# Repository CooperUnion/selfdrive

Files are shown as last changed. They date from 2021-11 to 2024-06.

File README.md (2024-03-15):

# selfdrive

> Autonomy Lab's monorepo

## Getting Started

`selfdrive` is a monorepo consisting of various Autonomy Lab projects
written in different languages with various dependencies. To avoid
dependency hell, we've opted to utilize the [Nix package manager] to
handle dependency resolution along with [direnv] to automate this
process.

### Installing Nix

Head over to <https://nixos.org/download> and proceed with the
installation for your platform. Once the process is complete, you'll
need to enable [Nix flakes] by adding the following to
`~/.config/nix/nix.conf`:

```
experimental-features = flakes nix-command
```

You'll also need to enable the unstable [channel] if you'd like to
install the latest versions of software:

```sh
$ nix-channel --add https://nixos.org/channels/nixpkgs-unstable nixpkgs
$ nix-channel --update
```

### Installing direnv

The easiest way to install [direnv] is through [`nix-env`]:

```sh
$ nix-env -iA nixpkgs.direnv
```

> Optionally, feel free to use your system's package manager to go
> through with the installation of [direnv].

Once installed, [hook direnv into your shell].

### Cloning `selfdrive`

Make sure that you've installed [Git] and [Git-LFS] before cloning.

Clone the repo:

```sh
$ git clone git@github.com:CooperUnion/selfdrive.git
```

Once cloned, make sure to initialize all the submodules:

```sh
$ git submodule update --init --recursive
```

We also recommend to configure [Git] to automatically update submodules
recursively:

```sh
$ git config --global submodule.recurse true
```

### Bootstrapping

Once everything's installed and set up, you can pass over the bootstrap
process to [direnv]:

```sh
$ direnv allow
```

If everything worked, you should be able to run [SCons] successfully:

```sh
$ scons --help
```

## Copyright & Licensing

Copyright (C) 2021--2024 Autonomy Lab

Distributed under the [GPLv3] only.

[channel]: https://nixos.wiki/wiki/Nix_channels
[direnv]: https://direnv.net/
[git]: https://git-scm.com/
[git-lfs]: https://git-lfs.com/
[gplv3]: LICENSE.md
[hook direnv into your shell]: https://direnv.net/docs/hook.html
[nix flakes]: https://nixos.wiki/wiki/Flakes
[nix package manager]: https://nixos.org/
[scons]: https://scons.org/
[`nix-env`]: https://nixos.org/manual/nix/stable/command-ref/nix-env

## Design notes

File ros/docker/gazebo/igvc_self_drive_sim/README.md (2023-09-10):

# IGVC Self-Drive Gazebo Simulator

This repository provides a Gazebo model of a Polaris GEM, as well as
worlds and models to simulate the tasks of the competition.

**If using ROS Noetic**, you need to clone the
[hector_models](https://github.com/tu-darmstadt-ros-pkg/hector_models.git)
and
[hector_gazebo](https://github.com/tu-darmstadt-ros-pkg/hector_gazebo.git)
repositories into the same workspace as this repositoriy.

After cloning into a ROS workspace along with `hector_gazebo` and
`hector_models` if necessary, run the following the command from the
root of the workspace to install additional ROS package dependencies to
make everything work correctly:

`rosdep install --from-paths src --ignore-src -r`

### Starting the Simulator

`roslaunch gazebo_ros empty_world.launch`

To load a custom Gazebo world file, pass its file path to the
`world_name` argument:

`roslaunch gazebo_ros empty_world.launch world_name:=<complete path to world file here\>`

Spawn the GEM model in Gazebo with `spawn_gem.launch` in the
`igvc_self_drive_gazebo` package:

`roslaunch igvc_self_drive_gazebo spawn_gem.launch`

The `spawn_gem.launch` file has arguments that allow the user to control
some aspects of the spawned GEM:

- `start_x`, `start_y`, `start_z`: The `x`, `y`, `z` position of the
  vehicle in Gazebo

- `start_yaw`: The direction the vehicle faces relative to the Gazebo
  world frame

- `twist_mode`: If true, the GEM subscribes to a `geometry_msgs/Twist`
  topic to move around the world. If false, it subscribes to individual
  actuator command topics. See the discussion of these modes below.

- `pub_tf`: If true, a ground truth TF transform from `world` frame to
  `base_footprint` frame is published

### Simulating IGVC Tasks

The `self_drive_tasks.world` file in the `igvc_self_drive_gazebo`
package simulates the specific tasks as described in the official rules
document, which can be found
\[[here](http://www.igvc.org/2018selfdriverules.pdf)\].

To load the world and spawn the vehicle at the starting point for a
particular task, run the corresponding launch file in the
`igvc_self_drive_gazebo` package. For example, to run task F3, the right
turn test where the vehicle has to stop at the intersection:

`roslaunch igvc_self_drive_gazebo f3_gazebo.launch`

At the moment, the F9 task is not implemented in the
`self_drive_tasks.world` Gazebo world, even though the launch file for
it exists.

### Sensor Data Topics

The following topics are published by Gazebo:

- `/fix`: GPS position given in latitude and longitude in the form of a
  `sensor_msgs/NavSatFix` message

- `/camera_front/image_raw/*`: Standard group of image topics from
  `image_proc`

- `/scan`: LIDAR scan data in the form of a `sensor_msgs/LaserScan`
  message

- `/twist`: The current measurement of the vehicle's speed and yaw rate
  in a `geometry_msgs/TwistStamped` message. The `linear.x` field
  contains the speed in m/s and `angular.z` contains the yaw rate in
  rad/s

- `/gear_state`: The current gear of the vehicle in a `std_msgs/UInt8`
  message:

  - 0 = Forward
  - 1 = Reverse

- `/sonar/*`: Group of 10 sonar sensor range measurement topics in
  separate `sensor_msgs/Range` messages. There are three sensors on the
  front of the vehicle, three on the rear, and two on either side.

### Controlling the Simulated Vehicle

The Gazebo GEM model can be controlled in two different modes:

- **Twist Mode:** Send a `geometry_msgs/Twist` message on the `/cmd_vel`
  topic with desired speed and yaw rate, and let the simulation generate
  the appropriate actuator commands.

- **Actuator Mode:** Send throttle, brake, steering, and gear actuator
  commands directly to the simulator.

#### Twist Mode (default)

The control mode is specified by setting the `twist_mode` argument to
the `spawn_gem.launch` file to true or false. This argument defaults to
true, so if you don't have to change anything to use Twist Mode.

The `linear.x` field of the user's `geometry_msgs/Twist` message should
contain the desired speed in m/s, and the `angular.z` field should
contain the desired yaw rate in rad/s.

#### Actuator Mode

By setting the `twist_mode` argument to false, the Gazebo plugin instead
subscribes to four separate actuator command topics so the user can
control them directly:

- `/throttle_cmd`: `std_msgs/Float64` topic containing commanded
  throttle percentage (0 to 1)

- `/brake_cmd`: `std_msgs/Float64` topic containing commanded brake
  torque in Newton-meters (0 to 1000)

- `/steering_cmd`: `std_msgs/Float64` topic containing commanded
  steering wheel angle in radians (-9.5 to +9.5)

- `/gear_cmd`: `std_msgs/UInt8` topic containing commanded gear, as
  controlled by the switch on the dashboard of the real vehicle:

  - 0 = Forward
  - 1 = Reverse

### Some Useful Kinematics Parameters

- Gear ratio between steering wheel and equivalent bicycle steer angle =
  17 : 1

- Wheelbase = 2.4 meters

- Track width = 1.2 meters

- Wheel radius = 0.36 meters

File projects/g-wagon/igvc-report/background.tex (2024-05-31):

\section{Background}

\subsection{Organization}

The team follows a vertically integrated structure, divided into three
disciplines consisting of three to five student groups, each led by a
subteam lead who facilitates weekly meetings. The subteams correspond
to abstract systems on the car: Hardware (Electrical + Mechanical),
Firmware, and Algorithms. In addition to weekly subteam meetings, we
hold weekly team meetings to keep everyone in the loop of new
developments and bi-weekly sprint meetings to establish tasks for our
bi-weekly test days.

The hardware subteam designs and assembles all expansion hats for the
Cooper Common Microcontroller Nodes (CCMNs), a custom
\texttt{\#coopermade} breakout board around the ESP32S3
microcontroller, to facilitate the needs of the Firmware subteam. In
addition to PCBs, the subteam is responsible for maintaining the power
distribution system of the car and designing mechanical components to
retrofit our vehicle.

Our Firmware subteam writes all our safety critical actuation code and
custom tooling to supplement software development. They aim to write
modular firmware, allowing for the fast extension of CCMNs attached to
hardware hats to specific hardware applications.

The algorithms subteam handles the perception and navigation of our
car. They create \& tune controllers, detect objects, perform
localization based on camera and encoder data, and generate paths given
all our component outputs.

\subsection{Design Assumptions \& Design Process}

Our design process revolves around ensuring our systems are safe and
easy to test in the cramped surroundings of the East Village in
downtown Manhattan. We try to make our systems as modular as possible
by breaking down every Autonomy Lab project into its various
components, allowing for overlap between different projects we may take
on. We host all our work in a publically available in a Git monorepo,
which is licensed under copyleft licenses to ensure free access to our
work to everyone. Maintaining a Git monorepo allows for easy
collaboration on components, simplifies code review, and lets us
accurately track changes to our work.

Due to Cooper's small size, it's easy for us to keep tabs on one
another to ensure things get done, but outside of meetings, we also
communicate using a Cooper-hosted instance of Matrix. We also believe
that maintaining good documentation is essential to avoid amassing
technical debt, so we keep a mix of public-facing documentation in our
monorepo and institution-specific documentation that does not make
sense to share outside Cooper.

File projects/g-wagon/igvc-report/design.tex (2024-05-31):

\section{Design}

\subsection{Mechanical}

Our mechanical design work revolved around retrofitting our vehicle so
that it's possible for it to drive itself. We added a gas-spring
emergency brake, a brake-by-cable system, spring-loaded rear encoders,
and a water-proof trunk to protect our power distribution system. In
addition to this, we designed various mounts for sensors,
microcontrollers, and our car computer. We lean towards aluminum and
steel for rigidity and machinability when designing mechanical
components to add to the car. We use 3D-printed components made from
PETG filament for anything not load-bearing, and when possible, we
drill mounting holes into our car's frame to mount components.

\subsubsection{Emergency Brake (Parking Brake)}

We mounted a gas spring rated for 20 lbs of force to our vehicle's
parking brake and we hold it in the armed position during operation
using an electromagnet. On each end of the spring, we bolted aluminum
extrusions between 3D-printed spaces that are free to rotate. We
machined brackets from 1/4" aluminum sheet metal to attach the spring
to the aluminum extrusions and hold any 3D-printed pieces to the car.

\begin{figure}[ht!]
  \centering
  
  \caption{CAD drawing of the parking brake assembly in the open position.}
\end{figure}

\subsubsection{Brake-by-Cable (BBC)}

We designed the Brake-By-Cable (BBC) system for fine control over
pressure in the master brake cylinder to better replicate a human
driver's control over the brake pedal. We designed the system based on
the constraint that it had to apply 100 lbs of force to displace the
brake pedal by two inches in less than a second. We designed the entire
assembly to fit in the small region between the master cylinder,
differential, and steering arms.

\begin{figure}[ht!]
  \centering
  
  \caption{CAD drawing of the BBC.}
\end{figure}

We chose a cable rated for 150 lbs to add a factor of safety. To reduce
our motor's torque requirements, we designed a 3:1 lever and machined
it from 1/4" steel. We connect the shorter side of the lever to the
brake pedal and the longer side to the DC motor. We machined a
three-inch steel pulley to be within the diameter recommended by the
manufacturer of our cable. We also machined an aluminum shaft coupler
to connect the top cable to our DC motor. For the DC motor, we chose it
such that the operating point of the system would be well below 20\% of
the motor's stall torque. Additionally, we added an extension spring to
the bottom of the lever to ensure that the cable stays in tension when
the motor releases the brake pedal.

We machined smaller pulleys from aluminum and used copper sleeves for
the cable terminations on the lever and brake pedal. Each termination
freely rotates using bronze bushing and shoulder bolts fastened to the
steel components. The large backplate covering the entire range of
motion of the lever is to ensure there are no pinch points in the
system. Each side of the lever also has an M6 shoulder bolt and a limit
switch so that our firmware can detect the end of the range of motion.

\subsubsection{Rear Encoder Mounts}

Critical for calculating odometry and velocity for the vehicle, this
year, we designed the rear encoders to have more precision and less
slip than the previous design. We designed and 3D printed a small wheel
(1.6 inches diameter) that directly attaches to the encoder shaft. This
wheel touches the inside of the car’s wheel so that we can measure the
tire's rotation. This geometry allows us to have over 30,000 counts per
tire rotation. To ensure that the encoder wheel does not slip and
maintains contact with the tire at all times, we designed a
spring-loaded bracket that connects with the previous encoder mount’s
bracket. The rotation point is an M8 shoulder bolt with thrust bearings
on each side of the 1/8th-inch aluminum bracket to ensure low-friction
rotation.

\begin{figure}[ht!]
  \centering
  
  \caption{CAD drawing of the rear encoders.}
\end{figure}

\subsubsection{Weather Proofing}

To protect the power distribution system from weather, we designed and
built a trunk that mounts to the back of the vehicle above the car
battery pack. We made the trunk's frame from 20mm aluminum extrusion,
held together with brackets made from a laser-cut 1/4" aluminum sheet.
We laser cut the trunk walls from 1/8" cast acrylic and fastened to the
aluminum extrusions. For ease of access, we mounted the circuit
breakers and under-voltage protection boards to the acrylic on top of
the trunk. We bolted the extrusion pieces to the chassis to ensure a
secure mount and used silicone caulk on the inside edges to ensure the
enclosure is weatherproof.

\newpage

\subsection{Electrical}

\begin{figure}[ht!]
  \centering
  
  \caption{Electric system diagram.}
\end{figure}

We distribute power from the 48V DC pack through circuit breakers,
fuses, under-voltage protection, and DC-to-DC converters to various
sensors, CCMNs, and our car computer. We daisy-chain all CCMNs with
Cat6A cables that supply 12V DC power and our car's CAN Bus. The boards
have voltage regulators, buck converters, and e-fuses for safe
operation and reverse polarity protection.

\subsubsection{Power Distribution System}

Four 12V DC, 120Ah AGM batteries connected in series power the car and
the electronic stack above. This setup yields us 5.8kWh, which lets the
car run for approximately six hours without needing to charge.

The DC motor controller (a Pololu G2 High-Power Motor Controller) draws
a lot of in-rush current when activated to drive the DC motor. To
prevent our DC motor controller from drawing too much current from the
DC-to-DC converters (causing their overcurrent protection to trip),
we've connected them to a battery charger, which charges a 12V battery
connected to our DC motor controller. We've also added a fast-burn 7A
fuse to the system to prevent damage if the motor stalls for an
extended period of time.

\subsubsection{Electronics Suite}

We connect a CCMN to an actuator, defining its node identity by its
expansion hat (if present). Each node interfaces with its actuator,
listening to control inputs over CAN and broadcasting senor values of
CAN. Webcams and our ZED2i are connected directly to our car computer.

\begin{itemize}
  \item \textbf{Accelerator:} sends two voltage signals directly to the throttle through relays to allow manual overrides.
  \item \textbf{BBC:} interfaces with a DC motor via a motor controller to perform pressure control and filters the pressure sensor before feeding it to the built-in ADC of the ESP32S3.
  \item \textbf{Encoders:} gets encoder ticks through level shifters.
  \item \textbf{Protoboard:} a generic expansion board for prototyping new expansion boards.
\end{itemize}

\subsubsection{Safety Devices}

Safety devices fall into two categories: mechanical/electrical devices
and software.

We use mechanical switches for e-stop buttons around the car to cut
power to our low-voltage system, effectively disabling all autonomous
aspects of our vehicle. Additionally, we've installed circuit breakers
around the car so that all systems have to be explicitly enabled by a
user, with the plus of adding over-current protection.

On the electrical side, we have ATC fuses in line with each device.
We've also added under-voltage protection to our 48V battery pack to
ensure its voltage does not fall below 40V and cause permanent damage.
Finally, each CCMN has a Schottky diode e-fuse on its input to allow
boards to survive accidental reverse input.

On the software side, we have a supervisor CCMN that ensures we never
latch in our vehicle's autonomous mode. This node inspects CAN messages
and, if all checks pass, can authorize other nodes on the CAN network
for autonomous control. This authorization has a TTL on the scale of
tens of milliseconds, meaning if any check fails, unauthorized
components of the system will exit autonomous control.

\subsection{Software}

Our software falls into two categories: Firmware and Algorithms.
Firmware creates the software interface between the hardware of the
car, while Algorithms generates inputs that we feed into our
Drive-By-Wire stack.

As an example, let's follow how a path generated by our Stanley
controller interacts with the car. We publish this path as a ROS topic
to another ROS node that interfaces with our CAN Bus. We then translate
this CAN message on our velocity controller CCMN using a PID controller
to a brake and throttle percentage. The throttle and BBC nodes then act
on these inputs only if authorized by our supervisor.

\subsubsection{Extracting Items from the Current Scene}

We handle object detection through a combination of a real-time
deep-learning model and an optical character recognition engine. We
chose Tesseract's OCR engine for reading road signs and only run it on
signs detected by our instance of the YOLOv8 model. We also use
point-cloud data from our ZED2i camera to compute the distance to
detected objects. Once an obstacle is detected, its location relative
to the vehicle gets published as a ROS topic.

We use two web cameras mounted on the A-pillars of our car for lane
detection. We use OpenCV to remove lens distortions and calculate a
linear mapping between pixels and physical distances. From here, we
threshold the image to detect white pixels and apply sliding windows to
find lane-line positions.

To detect which lane the car sits in, we compare the number of windows
with less than a determined number of white pixels from our sliding
windows. By nature, dashed lines have more empty windows, meaning we
can determine legal road maneuvers without a need for additional
localization.

We achieve \enquote{sensor fusion} using the
\texttt{ekf\_localization\_node} from the \texttt{robot\_localization}
ROS package. This node utilizes an extended Kalman filter to merge IMU
and encoder data for better estimates of our car's position.

\subsubsection{World Frame Representation}

We use odometry data from the \texttt{ekf\_localization\_node} to
obtain the position and orientation information of the vehicle in the
world frame. The ZED2i's point cloud data measures the vertical and
horizontal displacement of objects relative to the vehicle's location.
We then add the object's displacement relative to the vehicle's
location from its starting point to determine the object's location in
the world frame. We then feed this information into a state machine for
decision-making.

\begin{figure}[ht!]
  \centering
  
  \caption{
    We use Rviz2 to model vehicle dynamics at the control level: here,
    we demonstrate a generated path and the car position calculated
    using odometry from our rear encoders.
  }
\end{figure}

\subsubsection{Vehicle Operating Modes}

In self-driving mode, the vehicle operates in one of two states: lane
keeping or land changing. A land change generates paths to avoid road
obstructions by creating a clothoid path. We generate clothoid paths
based on the car's current position, orientation, endpoint, and final
orientation. Our vehicle switches operating modes based on the
conditions present.

\subsubsection{Trajectory Generation}

In lane-change mode, we operate purely on generated clothoid paths. A
lane change gets triggered by a detected object. Once detected, the
clothoid path gets generated and followed to avoid a collision.
Additionally, we generate trajectories to merge into different lanes or
to cross intersections.

\subsubsection{Trajectory Following Controls}

After researching trajectory-based controllers, and testing with
smaller steering robots, we determined that using a simplified bicycle
model and the Stanley geometric controller would suit our vehicle’s
needs for path following. The controller calculates a steering angle
based on two errors: the heading error, the yaw compared to the desired
heading of the path, and the cross-track error, the perpendicular
distance from the center of an axle to the path). We calculate the
steering angle using Equation \ref{eq:stanley}. Where \(\theta_e\) is
the heading error, \(t_e\) is the cross-track error, \(v\) is the
velocity, and \(k\) is the Stanley gain.

\begin{equation}
  \label{eq:stanley}
  \delta = \theta_e + \tan^{-1}\left(\frac{k t_e}{v}\right)
\end{equation}

\begin{figure}[ht!]
  \centering
  
  \caption{
    Kinematic bicycle model of a steering vehicle and the Stanley
    controller variables.
  }
\end{figure}

We have two methods of calculating the cross-track and heading errors
for the Stanley controller. For following generated paths, such as a
lane change, we use the encoders mounted to the rear tires to track the
vehicle’s current position and orientation. We calculate the Stanley
errors based on the car’s location and the nearest point of the path.

When following lane lines, when we have lines on both sides of the
vehicle, we use the web cameras mounted to the top of the vehicle to
detect the distance and angle of the lane lines relative to the car.

\subsubsection{Velocity Control}

On the Firmware side, once we receive a velocity command, the control
node determines if the car needs to accelerate or decelerate based on
the car’s current velocity. We feed the error between the desired and
actual velocities into a PID controller (the outer loop). If the car
needs to accelerate, we use a mapping between the desired acceleration
and throttle percentage and send the appropriate command to the
throttle node. If the car needs to decelerate, we use another mapping
between deceleration and brake pressure percentage and send that
command to the brake node.

On the BBC node, we implemented another PID loop (the inner loop),
which takes the error between the actual brake percentage (read by the
pressure transducer) and the desired brake percentage to calculate the
speed and direction of the BBC motor.

\begin{figure}[ht!]
  \centering
  
  \caption{Block diagram of our velocity controller.}
\end{figure}

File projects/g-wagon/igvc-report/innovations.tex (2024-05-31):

\section{Innovations}

This year, we decided to redesign our braking system and move to a
vision-based approach to path generation and object detection.

Our previous braking system, based around a Hydrastar trailer brake
system, was too powerful to allow consistent braking at low speeds. Our
new braking system, dubbed Brake-By-Cable, is our solution to add fine
control over the brakes. We installed a DC motor that rotates a pulley
so that a cable pulls on the brake pedal. We utilize a pressure and
current sensor as feedback for our control loop to allow for accurate
pressure control as requested by our vehicle controller.

To determine what lane our car is in and to calculate our heading and
cross-track errors, we've decided to use two cameras placed on each A
pillar of our vehicle. Since we can assume that our car operates on a
flat plane, we measure points along lane lines to create a trapezoidal
unwrap of each video feed, allowing us to use perspective transforms to
make an image where distance is a linear function of pixels.

\begin{figure}[ht!]
  \centering
  
  \caption{Fitted lane lines.}
\end{figure}

For our lane detection algorithm, we use a sliding window approach. We
divide the video feed from the pillar cameras into N windows, where we
threshold all white pixels within each window. We then use the
thresholded video feed to generate a polynomial model of the lane line.
This approach allows us to remove outliers and mitigate noise in our
input signals. Using these two polynomials, we can extract the
cross-track error (the distance from the center of the lane) by
comparing the distance between points on the polynomial and the front
axle. We can also extract the heading error (the angle relative to the
lane lines) by using a linear approximation of our generated
polynomials at the front axle and determining the deviation from the
vertical axis of the video feed.

\newpage

\begin{figure}[ht!]
  \centering
  
  \caption{Object detection demo.}
\end{figure}

We've also gone away with using a LIDAR sensor for object detection and
instead decided to use a deep learning model with a stereovision
camera. We're using Ultralytics's YOLOv8 model for its state-of-the-art
performance in real-time applications. We fine-tuned the model by
freezing the first ten layers and training on a small dataset of common
road obstructions and traffic signs.

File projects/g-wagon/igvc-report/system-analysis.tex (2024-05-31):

\section{System Analysis}

While testing things individually, it's easy to keep track of changes,
but once integrated into our system, it's easy to lose track of changes
and decisions. One example of this was during the development of the
BBC PCB. We broke the board into four main blocks: motor controller
logic, parking brake logic, pressure sensor data, and limit switches
for the lever's range of motion. However, when testing the entire
board, we found we would flip the polarity of certain pins, such as the
input to the motor, or flip which connectors went to the minimum limit
switch and the maximum limit switch.

The best way to prevent such mistakes is to create a more robust,
generalized system rather than case-by-case. For example, we can ensure
every wire has a proper visible label rather than memorizing its
location. Additionally, we can write out a simple checklist of what to
check before testing something. By creating a more robust system, it is
easy to prevent many of the smaller, simpler mistakes.

\subsection{Critical Hardware Failure}

One hardware failure that would prevent competition success is if an
ESP32S3 were to fail. The ESP32S3, a low-power microcontroller, limits
the amount of current it can supply. We maintain an external 12V
battery pack on the car because even though a CCMN can supply 12V, it's
limited to tens of milliamps. We handle this by using isolated circuits
to turn on/off the circuit i.e. using NMOS or PMOS transistors due to
their high input resistance as a switch or using a relay to keep the
two systems completely isolated.

\subsection{Software Development}

We store all code in a publically hosted monorepo on GitHub. We use Git
as it allows us to effectively work in parallel, while the monorepo
makes integration between various components straightforward. We
utilize GitHub features such as issues and pull requests to keep track
of problems with our code and encourage code review.

\subsection{Testing}

Before we test a particular algorithm or state machine on the car, and
because our team is limited in physical space to which we can test the
car, we test our ideas on smaller platforms, some of which we developed
within Autonomy Lab. Carrie is our designed in-house mini-car robot
platform for testing trajectory-following controllers. We tested and
tuned the Stanley geometric controller for following clothoid paths,
such as a complex path generated for parallel parking. We found the
Stanley controller to be an effective method of calculating a steering
angle for following a path. For testing with simplified dynamics, we
used a differential-drive TurtleBot platform. To initially test and
tune the OpenCV parameters for lane detection, we placed cameras on the
Turtlebot and added a simple controller to follow the lane lines.

\subsection{Physical Testing to Date}

We tested the BBC system by cycling the motor between the two limit
switches. The initial DC motor did not have enough torque and would
stall before reaching the maximum displacement of the brake pedal. We
sourced a more powerful DC motor with a higher stall torque, but this
larger motor can pull up to 25 Amps. To ensure the motor does not pull
too much current we installed a 7A fast-blow fuse on the battery
supplying power to the motor.

When measuring the pressure sensor output from the car, the original
data for the pressure sensor was from 0.7V to 2.0V. While this range of
values is valid for the ADC readings to the ESP32S3 (within 0.15V to
2.45V), there wouldn’t be enough precision to accurately calculate the
pressure percentage. By using a circuit that combines a non-inverting
OpAmp and a subtractor op amp, we simulated a circuit that linearly
remaps the pressure sensor range from 0.7V to 2.0V into 0.236V to
2.302V. In real-life however, we saw that the actual voltage range was
0.153V to 2.102V. This clearly demonstrates an example of when an ideal
simulation is different from a real-world implementation. The reason
for this difference comes from non-ideal components, device variations,
and parasitic capacitance and inductance throughout our circuit in the
op amps and resistors.

We tuned the inner PID loop for BBC using a pressure transducer and
recording the system's response time. We found that a high proportional
and small integral gain provided a fast response time with no
overshoot. When releasing the brake pedal before installing the spring,
the top cable would become loose and often fall off the pulley, causing
the cable to become plastically deformed. After installing the spring
to keep the lever and top cable in tension with the motor and pulley,
we found a great improvement in the response time and reliability of
the system.

For braking, once the inner loop's response was well tuned and we could
set and hold a desired braking percentage within 1 second, we
characterized the relationship between brake percent and deceleration.
First, we throttled the car to 10 mph, then set small increments of the
desired brake percent to measure deceleration using the encoders.

We ran tests using small increments in throttle percent to characterize
the acceleration-to-throttle percent relationship. We measured the
car's acceleration using the encoders mounted on the rear wheels.

To test the odometry for tracking position, we used Rviz2 to keep track
of the car's orientation and position relative to where it started in
the world frame. Since we could not test the throttle indoors, we
pushed the car while in neutral with the maximum steering angle to
travel in a circle to ensure the odometry returned to where we started.

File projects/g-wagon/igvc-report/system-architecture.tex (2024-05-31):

\section{System Architecture}

We like to think of our system as an hourglass. We aim to separate our
hardware components as much as possible from the algorithms we write,
where our car's firmware is the narrow bridge between these two worlds.

\vspace{1em}

Major hardware components include:
\begin{itemize}
  \item Our new Brake-By-Cable system
  \item Water-proof trunk for power distribution systems
  \item DC-DC converters
  \item Cooper Common Microcontroller Nodes
  \item A CAN Bus for node communication
  \item CCMN hats for our brakes, throttle, and encoders
  \item An ODrive for controlling our EPAS
\end{itemize}

Safety devices include:
\begin{itemize}
  \item Hardware E-STOPs around the car and inside the cabin
  \item ATC and glass tube fuses
  \item Circuit breakers
  \item Undervoltage protection
\end{itemize}

Major software modules include:
\begin{itemize}
  \item Shared firmware on all CCMNs
  \item OpenCAN for serialization/deserialization of CAN messages at cyclic
        rates
  \item Velocity and pressure controllers
  \item ROStouCAN for interfacing between nodes on our CAN Bus and our ROS
        nodes
  \item Lane detection algorithm
  \item Stanley controller for trajectory following
  \item A fine-tuned YOLO model for object detection
  \item State machines for state and event transitions based on the output of
        our object detection and lane detection
\end{itemize}

Even though we try to maintain our hourglass shape, it does not detract
from the close collaboration between our subteams. For example, our
Algorithms team needed more accurate braking on our vehicle this year,
so they met with the hardware subteam to make this possible. It was
then the responsibility of the hardware and firmware teams to work
together to ensure our new brake system performed better without
substantially changing how the system worked from the Algorithm
perspective.

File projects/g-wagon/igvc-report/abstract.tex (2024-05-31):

\begin{abstract}
  The Cooper IGVC Team is the primary research group of Cooper Union’s Autonomy
  Lab. As an organization, we're dedicated to cultivating autonomous
  vehicle research at our institution. We also work to uplift the Cooper
  community through the mentorship of underclassmen with the development
  of workshops to cultivate skills generalizable to complex projects
  outside of IGVC. We pride ourselves on building our car full-stack.
  Students in Autonomy Lab have designed all core mechanical, electronic,
  and software systems, all of which are open source.

  \vspace{1em}

  \noindent
  I, Michael Giglia, certify that the design and engineering of the vehicle by
  the current student team has been significant and equivalent to what
  might be awarded in a senior design course:

  \vspace{3em}

  \hrule

  \begin{center}
    
  \end{center}
\end{abstract}

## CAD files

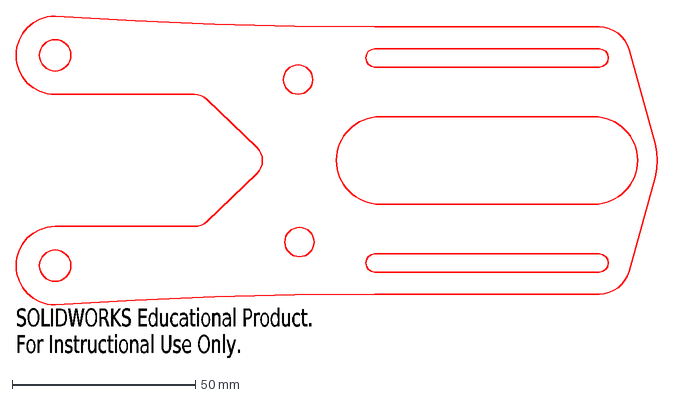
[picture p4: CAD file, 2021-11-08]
cad/encoderMount/ArmMount^EncoderMountV2.DXF
SOLIDWORKS Educational Product.
For Instructional Use Only.

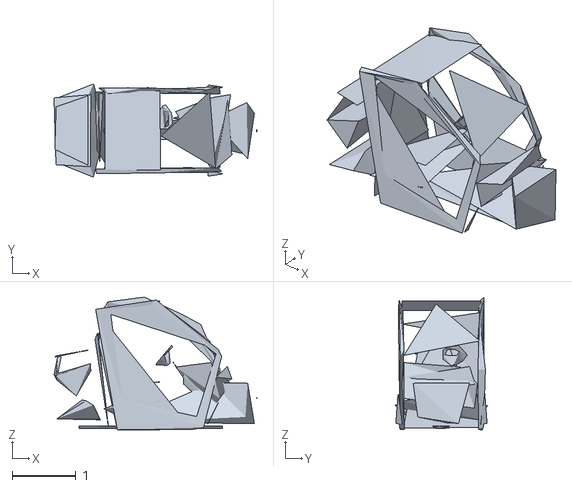
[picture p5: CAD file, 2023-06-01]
ros/docker/gazebo/igvc_self_drive_sim/igvc_self_drive_description/meshes/body_collision.stl
3.17 x 1.46 x 2.08

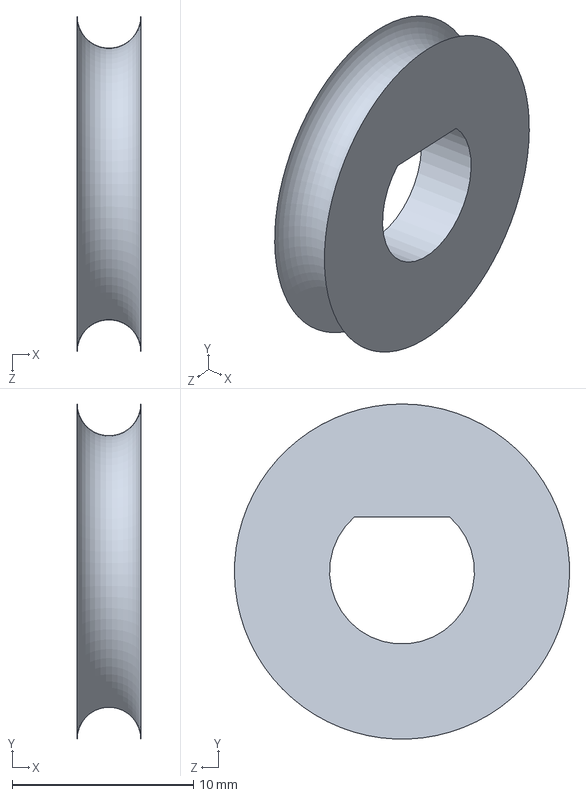
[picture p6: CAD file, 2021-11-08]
cad/encoderMount/wheel.SLDPRT
3.51 x 18.5 x 18.5 mm

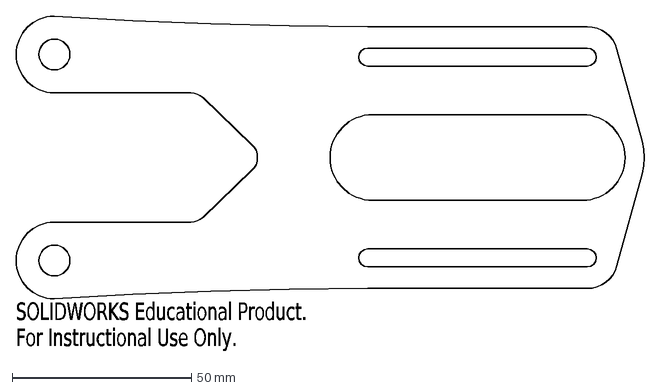
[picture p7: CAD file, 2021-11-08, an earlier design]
cad/encoderMount/ArmMount^EncoderMountV1.DXF
SOLIDWORKS Educational Product.
For Instructional Use Only.

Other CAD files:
cad/encoderMount/EncoderMountV2.SLDASM
cad/encoderMount/EncoderMountV1.SLDASM
ros/docker/gazebo/igvc_self_drive_sim/igvc_self_drive_gazebo/models/ocean/mesh.blend

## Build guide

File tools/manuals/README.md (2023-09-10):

# Notes

- The GEM service manual says -2019 and our GEM is a 2020 model, but the
  dealer says it's the same manual.

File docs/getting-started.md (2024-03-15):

# Getting Started

[`selfdrive`] is a rather *complicated* repo.

If you've never worked on a project of this scale, it can be daunting to
know where to start. The goal of this guide is to give you enough of a
foothold to start asking the right questions and to begin your adventure
here at Autonomy Lab.

## Fundamentals

Before we even get to cloning [`selfdrive`], you need to have the basic
mechanical skills required to traverse a shell. [MIT's Missing Semester]
serves as a great starting point for just this. The following table
lists the lectures you should watch if you plan to work on a specific
Autonomy Lab group:

| Lecture | Hardware | Firmware | Algorithms |
| --- | --- | --- | --- |
| [Course overview + the shell] | ✓\* | ✓\* | ✓\* |
| [Shell Tools and Scripting] | ✓ | ✓\* | ✓\* |
| [Editors (Vim)] | | | |
| [Data Wrangling] | | ✓ | ✓\* |
| [Command-line Environment] | ✓ | ✓\* | ✓\* |
| [Version Control (Git)] | ✓\* | ✓\* | ✓\* |
| [Debugging and Profiling] | | ✓ | ✓ |
| [Metaprogramming] | | ✓ | ✓ |
| [Security and Cryptography] | | | |
| [Potpourri] | | ✓ | ✓ |
| [Q&A] | | ✓ | ✓ |

> *Note: an `*` denotes you should also do the associated exercises.*

At a minimum, to clone [`selfdrive`], you should watch and do the
exercises for [Course overview + the shell] and [Version Control (Git)],
as these lectures provide you the fundamentals to hit the ground
running.

## System Configuration

Since [`selfdrive`] consists of software written in different
programming languages with a wide variety of dependencies, we've made an
effort to make getting your machine ready as painless as possible with
the [Nix package manager] and [direnv]. You can find cloning
instructions and system setup information on the repo's [`README.md`].

## Repo Layout

> Currently, [`selfdrive`] does not respect this structure. We're in the
> process of migrating over to this layout. Sorry for the time being.

```
selfdrive/
+-- can/
|   +-- network.yml
|
+-- docs/
|
+-- components/
|   +-- component/
|   |   +-- docs/
|   |   +-- src/
|   |   +-- component.toml
|   |
|   +-- ...
|
+-- lib/
|
+-- projects/
|   +-- project/
|   |   +-- docs/
|   |   +-- project.toml
|   |
|   +-- ...
|
+-- ...
```

There's quite a bit to unpack here, so let's get to it!

### [`components/`]

The [`components/`] directory contains components that serve as the
building blocks of a project.

Each component has a `docs/` directory that contains [symlinks] to
relevant documentation. These symlinks need to stay up to date as they
will automatically get triggered for manual review on pull requests to
ensure that documentation stays up to date. Having these symlinks also
ensures that anyone who wishes to get up to speed on a component has a
quick list of relevant documentation to read.

The `src` directory contains the source files. The contents and layout
of this directory highly depend on the component language(s) and use
case. It is best to see existing components to get a feel for it.

Finally, `component.toml` contains metadata related to the component.

### [`can/`]

[`can/`] describes the CAN networks of our projects. Here, you'll find
definitions for networks, messages, and signals for [OpenCAN] to
process.

### [`docs/`]

The [contributing guidelines] cover the structure for documentation. You
may notice that it closely follows the structure of [`selfdrive`]
itself.

### [`lib/`]

The [`lib/`] directory contains shared libraries used in components.
Since these are generalized pieces of software, the contents of each
directory can wildly vary. Feel free to explore these directories if
you're curious.

### [`projects/`]

The [`projects/`] directory contains projects that are composed of
various components. Like a component, each project has a `docs/`
directory with symlinks to relevant documentation and a `project.toml`
with related metadata.

### What About Everything Else?

It'd be impractical to cover every last file and directory in
[`selfdrive`]. Unfortunately, there's no shortcut to knowing where you
can find everything or how various bits of code interact, but there are
tools that can help!

- [`fd`]: a simple, fast and user-friendly alternative to `find`
- [`fzf`]: a command-line fuzzy finder
- [`rg`]: ripgrep recursively searches directories for a regex pattern

## So What's Next?

Now that you have a general idea of how [`selfdrive`] works, it's time
to move on to group-specific getting started guides. Feel free to move
along to these without finishing all of the suggested [missing semester]
lectures; however, understand they do nothing but benefit you!

[command-line environment]: https://missing.csail.mit.edu/2020/command-line/
[contributing guidelines]: contributing.md#directory-structure
[course overview + the shell]: https://missing.csail.mit.edu/2020/course-shell/
[data wrangling]: https://missing.csail.mit.edu/2020/data-wrangling/
[debugging and profiling]: https://missing.csail.mit.edu/2020/debugging-profiling/
[direnv]: https://direnv.net/
[editors (vim)]: https://missing.csail.mit.edu/2020/editors/
[metaprogramming]: https://missing.csail.mit.edu/2020/metaprogramming/
[missing semester]: https://missing.csail.mit.edu/
[mit's missing semester]: https://missing.csail.mit.edu/
[nix package manager]: https://nixos.org/
[opencan]: https://github.com/opencan
[potpourri]: https://missing.csail.mit.edu/2020/potpourri/
[q&a]: https://missing.csail.mit.edu/2020/qa/
[security and cryptography]: https://missing.csail.mit.edu/2020/security/
[shell tools and scripting]: https://missing.csail.mit.edu/2020/shell-tools/
[symlinks]: https://en.wikipedia.org/wiki/Symbolic_link
[version control (git)]: https://missing.csail.mit.edu/2020/version-control/
[`can/`]: https://github.com/CooperUnion/selfdrive/tree/dev/can
[`components/`]: https://github.com/CooperUnion/selfdrive/tree/dev/components
[`docs/`]: https://github.com/CooperUnion/selfdrive/tree/dev/docs
[`fd`]: https://github.com/sharkdp/fd
[`fzf`]: https://github.com/junegunn/fzf
[`lib/`]: https://github.com/CooperUnion/selfdrive/tree/dev/lib
[`projects/`]: https://github.com/CooperUnion/selfdrive/tree/dev/projects
[`readme.md`]: https://github.com/CooperUnion/selfdrive/blob/dev/README.md
[`rg`]: https://github.com/BurntSushi/ripgrep
[`selfdrive`]: https://github.com/CooperUnion/selfdrive

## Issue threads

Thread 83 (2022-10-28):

Missing EEPROM IC causes node to crash

dmezh, 2022-10-28:
We currently have EEPROM disabled because boards with a missing EEPROM crash. The EEPROM driver should be made resilient to this condition and indicate an error when needed.

dmezh, 2023-02-05:
See #113

jacobkoziej, 2023-11-01:
The following has been addressed by 3e016b3

Closed 2023-11-01.

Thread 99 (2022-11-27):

Report Core Temperature on CAN on Node v1.2

dmezh, 2022-11-27:
ESP32-S3 has a core temperature sensor: https://docs.espressif.com/projects/esp-idf/en/v4.4.2/esp32s3/api-reference/peripherals/temp_sensor.html

Report the temperature on CAN. Please ping me to discuss how to unify the CAN message between 1.1 and 1.2, since 1.1 doesn't have a temp sensor.

jacobkoziej, 2023-11-01:
Resolved in #130

Closed 2023-11-01.

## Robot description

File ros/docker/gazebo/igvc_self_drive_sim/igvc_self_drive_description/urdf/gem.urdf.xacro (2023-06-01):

<?xml version="1.0"?>

<robot name="gem" xmlns:xacro="http://ros.org/wiki/xacro">

  <xacro:include filename="$(find igvc_self_drive_description)/urdf/gem_gazebo.urdf.xacro"/>
  <xacro:include filename="$(find igvc_self_drive_description)/urdf/gem_sensors.urdf.xacro"/>

  <xacro:property name="half_front_track_width" value="0.6" />
  <xacro:property name="half_rear_track_width" value="0.6" />
  <xacro:property name="half_wheelbase" value="1.2" />
  <xacro:property name="wheel_radius" value="0.32" />
  <xacro:property name="wheel_thickness" value="0.17" />
  <xacro:property name="wheel_mass" value="10.0" />
  <xacro:property name="body_mass" value="544.0" />
  <xacro:property name="body_width" value="${2*half_rear_track_width}" />
  <xacro:property name="body_depth" value="${2*half_wheelbase + 0.8}" />
  <xacro:property name="body_length" value="0.6" />

  <xacro:macro name="rear_wheel" params="name x y z flip" >
    <link name="wheel_${name}" >
      <visual>
        <origin xyz="0 0 0" rpy="0 ${flip * pi - pi/2} 0" />
        <geometry>
          <mesh filename="package://igvc_self_drive_description/meshes/wheel.dae" scale="2.54 2.54 2.54" />
        </geometry>
      </visual>

      <collision>
        <geometry>
          <cylinder radius="${wheel_radius}" length="${wheel_thickness}" />
        </geometry>
      </collision>

      <inertial>
        <origin xyz="0 0 0" rpy="0 0 0"/>
        <mass value="${wheel_mass}"/>
        <inertia ixx="${wheel_mass/12*(3*wheel_radius*wheel_radius + wheel_thickness*wheel_thickness)}" ixy="0" ixz="0" iyy="${wheel_mass/12*(3*wheel_radius*wheel_radius + wheel_thickness*wheel_thickness)}" iyz="0" izz="${wheel_mass/2 * wheel_radius*wheel_radius}"/>
      </inertial>

    </link>
    <joint name="wheel_${name}_joint" type="continuous" >
      <parent link="base_link" />
      <child link="wheel_${name}" />
      <origin xyz="${x} ${y} ${z}" rpy="-1.57079632679 0 0" />
      <axis xyz="0 0 1" />
      <limit effort="1000.0" velocity="22.0" />
    </joint>
  </xacro:macro>

  <xacro:macro name="front_wheel" params="name x y z flip" >
    <link name="wheel_${name}" >
      <visual>
        <origin xyz="0 0 0" rpy="0 ${flip * pi - pi/2} 0" />
        <geometry>
          <mesh filename="package://igvc_self_drive_description/meshes/wheel.dae" scale="2.54 2.54 2.54" />
        </geometry>
      </visual>

      <collision>
        <geometry>
          <cylinder radius="${wheel_radius}" length="${wheel_thickness}" />
        </geometry>
      </collision>

      <inertial>
        <origin xyz="0 0 0" rpy="0 0 0"/>
        <mass value="${wheel_mass}"/>
        <inertia ixx="${wheel_mass/12*(3*wheel_radius*wheel_radius + wheel_thickness*wheel_thickness)}" ixy="0" ixz="0" iyy="${wheel_mass/12*(3*wheel_radius*wheel_radius + wheel_thickness*wheel_thickness)}" iyz="0" izz="${wheel_mass/2 * wheel_radius*wheel_radius}"/>
      </inertial>
    </link>

    <link name="steer_${name}" >
      <inertial>
        <origin xyz="0 0 0" rpy="0 0 0"/>
        <mass value="20.0"/>
        <inertia ixx="0.1" ixy="0" ixz="0" iyy="0.1" iyz="0" izz="0.1"/>
      </inertial>
    </link>

    <joint name="steer_${name}_joint" type="revolute" >
      <parent link="base_link" />
      <child link="steer_${name}" />
      <origin xyz="${x} ${y} ${z}" rpy="0 0 0" />
      <axis xyz="0 0 1" />
      <limit upper="0.6" lower="-0.6" effort="0.0" velocity="0.0" />
    </joint>

    <joint name="wheel_${name}_joint" type="continuous" >
      <parent link="steer_${name}" />
      <child link="wheel_${name}" />
      <origin xyz="0 0 0" rpy="-1.57079632679 0 0" />
      <axis xyz="0 0 1" />
      <limit effort="1000.0" velocity="22.0" />
    </joint>
  </xacro:macro>

  <link name="base_footprint">
  </link>

  <link name="base_link">
    <inertial>
      <origin xyz="0 0 0.75" rpy="0 0 0"/>
      <mass value="${body_mass}"/>
      <inertia ixx="${body_mass/12 * (body_width*body_width + body_length*body_length)}" ixy="0" ixz="0" iyy="${body_mass/12 * (body_length*body_length + body_depth*body_depth)}" iyz="0" izz="${body_mass/12 * (body_width*body_width + body_depth*body_depth)}"/>
    </inertial>
    <visual>
      <origin xyz="-0.22 0 0.07" rpy="0 0 0"/>
      <geometry>
        <mesh filename="package://igvc_self_drive_description/meshes/body.dae" scale="1 1 1" />
      </geometry>
    </visual>
    <collision>
      <origin xyz="-0.22 0 0.07" rpy="0 0 0"/>
      <geometry>
        <mesh filename="package://igvc_self_drive_description/meshes/body_collision.stl" scale="1 1 1" />
      </geometry>
    </collision>
  </link>

  <xacro:rear_wheel name="rl" x="${-half_wheelbase}" y="${half_rear_track_width}" z="0" flip="1" />
  <xacro:rear_wheel name="rr" x="${-half_wheelbase}" y="${-half_rear_track_width}" z="0" flip="0" />
  <xacro:front_wheel name="fl" x="${half_wheelbase}" y="${half_front_track_width}" z="0" flip="1" />
  <xacro:front_wheel name="fr" x="${half_wheelbase}" y="${-half_front_track_width}" z="0" flip="0" />

  <joint name="base_link_joint" type="fixed">
    <origin xyz="${half_wheelbase} 0 ${wheel_radius}" rpy="0 0 0"/>
    <parent link="base_footprint"/>
    <child link="base_link"/>
  </joint>

</robot>

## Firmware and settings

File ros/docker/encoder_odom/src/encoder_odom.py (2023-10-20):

#!/usr/bin/env python3

import ctypes

import rospy
import tf2_ros
import tf_conversions


from math import (
    cos,
    sin,
)

from geometry_msgs.msg import (
    Point,
    Pose,
    Quaternion,
    TransformStamped,
    Twist,
    Vector3,
)

from std_msgs.msg import UInt16MultiArray, String
from nav_msgs.msg import Odometry


class Subscribe:
    def __init__(self):
        self.left_ticks: ctypes.c_uint16 = 0
        self.right_ticks: ctypes.c_uint16 = 0
        rospy.Subscriber('/encoder_ticks', UInt16MultiArray, self.callback)

    def callback(self, msg):
        self.left_ticks = msg.data[0]
        self.right_ticks = msg.data[1]


# vx and vth come from encoders
# Not sure whether to use EPAS encoder for th or use encoders for vth to calculate th
# vy might always be zero
class Encoder_Odom:
    def __init__(self):
        self.sub = Subscribe()
        self.broadcaster = tf2_ros.TransformBroadcaster()
        self.rate = rospy.Rate(100)
        self.odom_pub = rospy.Publisher(
            '/encoder_odom', Odometry, queue_size=2
        )
        self.odom_msg = Odometry()

        self.x = 0.0
        self.y = 0.0
        self.th = 0.0

        self.vx = 0.0
        self.vy = 0.0
        self.vth = 0.0

        self.dt = 0.0
        self.delta_x = 0.0
        self.delta_y = 0.0
        self.delta_th = 0.0

        self.delta_left = 0
        self.delta_right = 0
        self.v_left = 0.0
        self.v_right = 0.0

        # starting the node at 0 ticks might cause a problem with absolute encoders???
        self.prev_left_ticks: ctypes.c_uint16 = 0
        self.prev_right_ticks: ctypes.c_uint16 = 0

    def send_transform(self, current_time):
        t = TransformStamped()

        # double check this
        t.header.stamp = current_time
        t.header.frame_id = "odom"
        t.child_frame_id = "base_link"
        t.transform.translation.x = self.x
        t.transform.translation.y = self.y
        t.transform.translation.z = 0.0
        self.q = tf_conversions.transformations.quaternion_from_euler(
            0, 0, self.th
        )
        t.transform.rotation.x = self.q[0]
        t.transform.rotation.y = self.q[1]
        t.transform.rotation.z = self.q[2]
        t.transform.rotation.w = self.q[3]

        self.broadcaster.sendTransform(t)

    def calc_odom(self, current_time, last_time):
        # Car Variables
        wheel_radius = 0.3302  # 13 inch ~= 0.3302 meter  # noqa: F841
        circumference = 1.899156
        enc_res = 65536
        tick_distance = circumference / enc_res
        wheel_spacing = 1.27  # Approximately 50 inch ~= 1.27 meter

        # Overflow condition for unsigned integer subtraction
        # if(self.sub.left_ticks > self.prev_left_ticks):
        #     self.delta_left = self.sub.left_ticks - self.prev_left_ticks
        # else:
        #     self.delta_left = self.prev_left_ticks - self.sub.left_ticks

        # if(self.sub.right_ticks > self.prev_right_ticks):
        #     self.delta_right = self.sub.right_ticks - self.prev_right_ticks
        # else:
        #     self.delta_right = self.prev_right_ticks - self.sub.right_ticks

        self.delta_left: ctypes.c_int16 = ctypes.c_int16(
            self.sub.left_ticks - self.prev_left_ticks
        )
        self.delta_right: ctypes.c_int16 = ctypes.c_int16(
            self.sub.right_ticks - self.prev_right_ticks
        )

        self.v_left = (
            -(float(self.delta_left.value) * tick_distance)
            / (current_time - last_time).to_sec()
        )
        self.v_right = (float(self.delta_right.value) * tick_distance) / (
            current_time - last_time
        ).to_sec()
        print(f"L: {self.sub.left_ticks}, R: {self.sub.right_ticks}")

        # 10 is a scaling factor used to characterize system
        self.vx = (self.v_right + self.v_left) / 2
        self.vth = (self.v_right - self.v_left) / wheel_spacing

        self.dt = (current_time - last_time).to_sec()
        self.delta_x = (
            self.vx * cos(self.th) - self.vy * sin(self.th)
        ) * self.dt
        self.delta_y = (
            self.vx * sin(self.th) + self.vy * cos(self.th)
        ) * self.dt
        self.delta_th = self.vth * self.dt

        self.x += self.delta_x
        self.y += self.delta_y
        self.th += self.delta_th

        self.send_transform(current_time)

        self.prev_left_ticks = self.sub.left_ticks
        self.prev_right_ticks = self.sub.right_ticks

        # format Odom message
        self.odom_msg.header.stamp = current_time
        self.odom_msg.header.frame_id = "odom"

        # set the position
        self.odom_msg.pose.pose = Pose(
            Point(encoder_odom.x, encoder_odom.y, 0.0),
            Quaternion(*encoder_odom.q),
        )

        # set the velocity
        self.odom_msg.child_frame_id = "base_link"
        self.odom_msg.twist.twist = Twist(
            Vector3(encoder_odom.vx, encoder_odom.vy, 0),
            Vector3(0, 0, encoder_odom.vth),
        )

        self.odom_pub.publish(self.odom_msg)
        self.rate.sleep()


if __name__ == '__main__':
    rospy.init_node('encoder_odom', anonymous=True, log_level=rospy.DEBUG)
    pub = rospy.Publisher('/encoder_string', String)
    encoder_odom = Encoder_Odom()

    current_time = rospy.Time.now()
    last_time = rospy.Time.now()

    while not rospy.is_shutdown():
        current_time = rospy.Time.now()

        encoder_odom.calc_odom(current_time, last_time)

        last_time = current_time

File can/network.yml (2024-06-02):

---

bitrate: 500000

message_templates:
  - DBWNodeInfo:
      cycletime: 1000
      signals:
        - gitHash:
            description: Githash of the currently-running firmware.
            width: 32
        - gitDirty:
            description: Repository was dirty at build time.
            width: 1
        - eepromIdentity:
            description: EEPROM identity.
            width: 6

  - DBWNodeStatus:
      cycletime: 100

      signals:
        - sysStatus:
            description: Status of the node.
            enumerated_values:
              - UNDEF
              - INIT
              - IDLE
              - ACTIVE
              - LOST_CAN
              - BAD
              - ESTOP
        - requestedSysStatus:
            description: Requested node status.
            enumerated_values:
              - UNDEF
              - INIT
              - IDLE
              - ACTIVE
              - LOST_CAN
              - BAD
              - ESTOP
        - temperature:
            description: Core temperature in Celsius
            width: 7
            offset: 31
        - counter:
            description: Counter for fun.
            width: 8
        - resetReason:
            description: Reset reason.
            enumerated_values:
              - POWERON
              - SW_RESET
              - WATCHDOG_RESET
              - UNKNOWN
        - esp32ResetReasonCode:
            description: ESP32 reset reason code (enum RESET_REASON)
            width: 5

  - DBWVelocityCommand:
      cycletime: 10

      signals:
        - brakePercent:
            description: Brake percentage.
            # mimumum: 0.0
            # maximum: 100.0
            unit: percent
            width: 10
            scale: 0.1
        - throttlePercent:
            description: Throttle percentage.
            # minimum: 0.0
            # maximum: 100.0
            unit: percent
            width: 10
            scale: 0.1

  - EncoderData:
      cycletime: 10
      signals:
        - encoderLeft:
            description: >
              Left encoder pulses (continuous, bidirectional, and overflowing).
            width: 16
        - encoderRight:
            description: >
              Right encoder pulses (continuous, bidirectional, and overflowing).
            width: 16

  - PIDGains:
      signals:
        - gainKp:
            description: Kp gain.
            width: 16
            scale: 0.001

        - gainKi:
            description: Ki gain.
            width: 16
            scale: 0.001

        - gainKd:
            description: Kd gain.
            width: 17
            twos_complement: true
            scale: 0.001

  - UpdateControl:
      cycletime: 20

      signals:
        - updateSizeBytes:
            description: Total update binary size in bytes.
            width: 24
        - currentIsoTpChunk:
            description: Current isotp 4095-byte chunk.
            width: 12

  - BlStatus:
      cycletime: 20

      signals:
        - state:
            enumerated_values:
              - AWAIT_TRIGGER
              - RECV_CHUNK
              - CHECK_DESC
              - COMMIT_CHUNK
              - FINALIZE
              - REBOOT_FW
              - FAULT
              - RESET

nodes:
  - BBC:
      rx:
        - CTRL_VelocityCommand
        - DBW_ESTOP
        - DBW_SetBBCGains
        - DBW_VelocityCommand
        - SUP_Authorization
        - UPD_UpdateControl_BBC  # bootloader
      messages:
        - NodeInfo:
            from_template: DBWNodeInfo
            id: 0xD2

        - NodeStatus:
            from_template: DBWNodeStatus
            id: 0xE2

        - BrakeData:
            id: 0x11
            cycletime: 10

            signals:
              - motorPercent:
                  description: Percentage PWM to motor, controller output.
                  # minimum: 0.0
                  # maximum: 100.0
                  width: 10
                  unit: percent
                  scale: 0.1

              - pressurePercent:
                  description: Pressure percentage.
                  # minimum: 0.0
                  # maximum: 100.0
                  width: 10
                  unit: percent
                  scale: 0.1

              - adcNormalizedRaw:
                  description: ADC reading (raw).
                  # minimum: 0.0
                  # maximum: 100.0
                  width: 10
                  unit: percent
                  scale: 0.1

              - adcNormalizedFiltered:
                  description: ADC reading (filtered).
                  # minimum: 0.0
                  # maximum: 100.0
                  width: 10
                  unit: percent
                  scale: 0.1

              - limitSwitchMax:
                  description: status of forwards switch
                  width: 1

              - limitSwitchMin:
                  description: status of backwards switch
                  width: 1
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

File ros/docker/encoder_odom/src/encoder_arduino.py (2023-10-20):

#!/usr/bin/env python3

import pyfirmata
import rospy
import tf2_ros


from math import (
    cos,
    sin,
)

from geometry_msgs.msg import (
    Point,
    Pose,
    Quaternion,
    Twist,
    Vector3,
)
from nav_msgs.msg import Odometry


# The Odometry message type contains the following messages:
# header (Coordinate frame for the pose)
# child_frame_id (Coordinate frame for the twist)
# pose (with covariance if provided by ekf)
# twist (with covariance if provided by ekf)
class Publish:
    def __init__(self):
        self.odom = rospy.Publisher('/encoder_odom', Odometry, queue_size=2)
        # increase rate for RTABmap
        self.rate = rospy.Rate(1.0)

    def publish(self, data):
        while not rospy.is_shutdown():
            self.odom.publish(data)


# vx and vth come from encoders
# Not sure whether to use EPAS encoder for th or use encoders for vth to calculate th
# vy might always be zero
class Encoder_Odom:
    def __init__(self):
        self.sub = Subscribe()  # noqa: F821
        self.broadcaster = tf2_ros.TransformBroadcaster()

        self.x = 0.0
        self.y = 0.0
        self.th = 0.0

        self.vx = 0.0
        self.vy = 0.0
        self.vth = 0.0

        self.dt = 0.0
        self.delta_x = 0.0
        self.delta_y = 0.0
        self.delta_th = 0.0

    def calc_odom(self, enc_vel, enc_omega, current_time, last_time):
        # Change these lines
        self.vx = enc_vel
        self.vth = enc_omega

        self.dt = (current_time - last_time).to_sec()
        self.delta_x = (
            self.vx * cos(self.th) - self.vy * sin(self.th)
        ) * self.dt
        self.delta_y = (
            self.vx * sin(self.th) + self.vy * cos(self.th)
        ) * self.dt
        self.delta_th = self.vth * self.dt

        self.x += self.delta_x
        self.y += self.delta_y
        self.th += self.delta_th

        self.odom_quat = tf2_ros.transformations.quaternion_from_euler(
            0, 0, self.th
        )
        self.broadcaster.sendTransform(
            (self.x, self.y, 0.0),
            self.odom_quat,
            current_time,
            "base_link",
            "odom",
        )


# Encoder variables
wheel_radius = 1.0
circumfrence = 3.1415926 * 2 * wheel_radius
enc_res = 2048
tick_distance = circumfrence / enc_res
wheel_spacing = 1.0
prev_left_ticks = 0
prev_right_ticks = 0

# Initalize Arduino board variables
board = pyfirmata.Arduino('/dev/ttyACM0')
left_enc_pin = 5
right_enc_pin = 6
# Used to continuously read values from Arduino board
it = pyfirmata.util.Iterator(board)
it.start()

board.analog[left_enc_pin].mode = pyfirmata.INPUT
board.analog[right_enc_pin].mode = pyfirmata.INPUT

# Initialize time variables
current_time = rospy.Time.now()
last_time = rospy.Time.now()

# Not sure whether or not to initialize outside of the loop
rospy.init_node('encoder_odom', anonymous=True)
encoder_odom = Encoder_Odom()

if __name__ == '__main__':
    # rospy.init_node('encoder_odom', anonymous=True)

    current_time = rospy.Time.now()
    left_ticks = board.analog[left_enc_pin].read
    right_ticks = board.analog[right_enc_pin].read

    # Not sure if we need to include sleep time since the measurements are limited by the rate of the publisher
    # time.sleep(0.1)
    delta_left = left_ticks - prev_left_ticks
    delta_right = right_ticks - prev_right_ticks

    v_left = (delta_left * tick_distance) / (current_time - last_time).to_sec()
    v_right = (delta_right * tick_distance) / (
        current_time - last_time
    ).to_sec()

    # 10 is a scaling factor used to characterize system
    enc_vel = ((v_right + v_left) / 2) * 10
    enc_omega = ((v_right - v_left) / wheel_spacing) * 10

    encoder_odom.calc_odom(enc_vel, enc_omega, current_time, last_time)

    odom_msg = Odometry()
    odom_msg.header.stamp = current_time
    odom_msg.header.frame_id = "odom"

    # set the position
    odom_msg.pose.pose = Pose(
        Point(encoder_odom.x, encoder_odom.y, 0.0),
        Quaternion(*encoder_odom.odom_quat),
    )

    # set the velocity
    odom_msg.child_frame_id = "base_link"
    odom_msg.twist.twist = Twist(
        Vector3(encoder_odom.vx, encoder_odom.vy, 0),
        Vector3(0, 0, encoder_odom.vth),
    )

    last_time = current_time
    prev_left_ticks = left_ticks
    prev_right_ticks = right_ticks
    rospy.spin()

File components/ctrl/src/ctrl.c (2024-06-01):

#include "ctrl.h"

#include "firmware-base/state-machine.h"
#include <driver/gpio.h>
#include <ember_common.h>
#include <ember_taskglue.h>
#include <esp_attr.h>
#include <freertos/FreeRTOS.h>
#include <freertos/task.h>
#include <opencan_rx.h>
#include <opencan_tx.h>
#include <selfdrive/pid.h>

#define ENCODER0_CHAN_A 3
#define ENCODER0_CHAN_B 4
#define ENCODER1_CHAN_A 36
#define ENCODER1_CHAN_B 35

#define ESP_INTR_FLAG_DEFAULT 0

#define ENCODER_MAX_TICKS	   400	// slightly over 5mph
#define ENCODER_TICKS_PER_ROTATION 30536

#define WHEEL_CIRCUMFERENCE_M 1.7954

#define METERS_PER_TICK \
	((float) WHEEL_CIRCUMFERENCE_M / (float) ENCODER_TICKS_PER_ROTATION)

#define ACCELERATION_TO_THROTTLE_PERCENT_LINEAR_MAPPING	       40.97
#define ACCELERATION_TO_THROTTLE_PERCENT_LINEAR_MAPPING_OFFSET 0
#define ACCELERATION_TO_BRAKE_PERCENT_LINEAR_MAPPING	       -36.60
#define ACCELERATION_TO_BRAKE_PERCENT_LINEAR_MAPPING_OFFSET    0

#define ACCELERATION_TO_THROTTLE_PERCENT(x)                      \
	(((x) * ACCELERATION_TO_THROTTLE_PERCENT_LINEAR_MAPPING) \
		+ ACCELERATION_TO_THROTTLE_PERCENT_LINEAR_MAPPING_OFFSET)

#define ACCELERATION_TO_BRAKE_PERCENT(x)                      \
	(((x) * ACCELERATION_TO_BRAKE_PERCENT_LINEAR_MAPPING) \
		+ ACCELERATION_TO_BRAKE_PERCENT_LINEAR_MAPPING_OFFSET)

#define AVERAGE_TICKS_SAMPLES 4

#define KP    0.35
#define KI    0.035
#define KD    0.42
#define SIGMA 1.00

#define PID_LOWER_LIMIT	   -5
#define PID_UPPER_LIMIT	   2
#define PID_DEADBAND_LOWER 0
#define PID_DEADBAND_UPPER 0

static void ctrl_init();
static void ctrl_100Hz();
static void calculate_average_velocity(
	int16_t left_delta, int16_t right_delta);
static void encoder0_chan_a(void *arg);
static void encoder0_chan_b(void *arg);
static void encoder1_chan_a(void *arg);
static void encoder1_chan_b(void *arg);
static void velocity_control(
	float desired_velocity, float desired_acceleration);

static volatile uint16_t pulse_cnt[2];
static bool		 speed_alarm;
static uint8_t		 brake_percent;
static uint8_t		 throttle_percent;

static float average_velocity;
static float desired_acceleration;

static selfdrive_pid_t pid;
static bool	       setpoint_reset;

ember_rate_funcs_S module_rf = {
	.call_init  = ctrl_init,
	.call_100Hz = ctrl_100Hz,
};

static void ctrl_init()
{
	gpio_set_direction(ENCODER0_CHAN_A, GPIO_MODE_INPUT);
	gpio_set_direction(ENCODER0_CHAN_B, GPIO_MODE_INPUT);
	gpio_set_direction(ENCODER1_CHAN_A, GPIO_MODE_INPUT);
	gpio_set_direction(ENCODER1_CHAN_B, GPIO_MODE_INPUT);

	gpio_set_intr_type(ENCODER0_CHAN_A, GPIO_INTR_ANYEDGE);
	gpio_set_intr_type(ENCODER0_CHAN_B, GPIO_INTR_ANYEDGE);
	gpio_set_intr_type(ENCODER1_CHAN_A, GPIO_INTR_ANYEDGE);
	gpio_set_intr_type(ENCODER1_CHAN_B, GPIO_INTR_ANYEDGE);

	gpio_install_isr_service(ESP_INTR_FLAG_DEFAULT);

	gpio_isr_handler_add(ENCODER0_CHAN_A, encoder0_chan_a, NULL);
	gpio_isr_handler_add(ENCODER0_CHAN_B, encoder0_chan_b, NULL);
	gpio_isr_handler_add(ENCODER1_CHAN_A, encoder1_chan_a, NULL);
	gpio_isr_handler_add(ENCODER1_CHAN_B, encoder1_chan_b, NULL);

	selfdrive_pid_init(&pid,
		KP,
		KI,
		KD,
		0.01,
		PID_LOWER_LIMIT,
		PID_UPPER_LIMIT,
		SIGMA);

	selfdrive_pid_set_deadbands(
		&pid, PID_DEADBAND_LOWER, PID_DEADBAND_UPPER);
}

static void ctrl_100Hz()
{
	static uint16_t prv_pulse_cnt[2];

	const uint16_t cur_pulse_cnt[2] = {pulse_cnt[0], pulse_cnt[1]};

	const int16_t left_delta  = cur_pulse_cnt[0] - prv_pulse_cnt[0];
	const int16_t right_delta = cur_pulse_cnt[1] - prv_pulse_cnt[1];

	prv_pulse_cnt[0] = cur_pulse_cnt[0];
	prv_pulse_cnt[1] = cur_pulse_cnt[1];

	calculate_average_velocity(left_delta, right_delta);

	// check if we're over the speed limit and
	// go into the ESTOP state if that's the case
	if ((base_get_state() == SYS_STATE_DBW_ACTIVE)
		&& ((ABS(left_delta) >= ENCODER_MAX_TICKS)
			|| (ABS(right_delta) >= ENCODER_MAX_TICKS))) {
		brake_percent	 = 0;
		throttle_percent = 0;

		speed_alarm = true;
		base_request_state(SYS_STATE_ESTOP);

		return;
	}

	speed_alarm = false;

	/*
	 * We want to set brake and throttle percentages based on either a
	 * raw or normal velocity command.  Ideally, a raw velocity command
	 * would not be sent when a regular velocity command is being sent
	 * and vice-versa.  To avoid this situation, we give the raw
	 * velocity command priority when setting percentages.
	 */
	if (CANRX_is_message_DBW_RawVelocityCommand_ok()) {
		base_request_state(SYS_STATE_DBW_ACTIVE);

		taskDISABLE_INTERRUPTS();
		brake_percent	 = CANRX_get_DBW_brakePercent();
		throttle_percent = CANRX_get_DBW_throttlePercent();
		taskENABLE_INTERRUPTS();

		return;
	}

	if (CANRX_is_message_DBW_VelocityCommand_ok()) {
		base_request_state(SYS_STATE_DBW_ACTIVE);

		float current_velocity = average_velocity;
		float desired_velocity = CANRX_get_DBW_linearVelocity();

		if (setpoint_reset) {
			selfdrive_pid_setpoint_reset(
				&pid, desired_velocity, current_velocity);
			setpoint_reset = false;
		}

		desired_acceleration = selfdrive_pid_step(
			&pid, desired_velocity, current_velocity);

		velocity_control(desired_velocity, desired_acceleration);

		return;
	}

	base_request_state(SYS_STATE_IDLE);

	brake_percent	 = 0;
	throttle_percent = 0;
	setpoint_reset	 = true;
}

static void calculate_average_velocity(int16_t left_delta, int16_t right_delta)
{
	static size_t  index;
	static int32_t average_ticks_sum;
	static int32_t average_ticks_buf[AVERAGE_TICKS_SAMPLES];

	// remove stale value
	average_ticks_sum -= average_ticks_buf[index];

	average_ticks_buf[index]  = (left_delta + right_delta) / 2;
	average_ticks_sum	 += average_ticks_buf[index];

	index = (index + 1) % AVERAGE_TICKS_SAMPLES;

	int16_t ticks_10ms = average_ticks_sum / AVERAGE_TICKS_SAMPLES;


	// * 100 is to go from 10ms to 1s
	average_velocity = ticks_10ms * METERS_PER_TICK * 100;
}

static void IRAM_ATTR encoder0_chan_a(void *arg)
{
	(void) arg;

	const uint32_t chan_a = gpio_get_level(ENCODER0_CHAN_A);
	const uint32_t chan_b = gpio_get_level(ENCODER0_CHAN_B);

	if (chan_a) {
		if (chan_b) {
			--pulse_cnt[0];
		} else {
			++pulse_cnt[0];
		}
	} else {
		if (chan_b) {
			++pulse_cnt[0];
		} else {
			--pulse_cnt[0];
		}
	}
}

static void IRAM_ATTR encoder0_chan_b(void *arg)
{
	(void) arg;

	const uint32_t chan_a = gpio_get_level(ENCODER0_CHAN_A);
	const uint32_t chan_b = gpio_get_level(ENCODER0_CHAN_B);

	if (chan_b) {
		if (chan_a) {
			++pulse_cnt[0];
		} else {
			--pulse_cnt[0];
		}
	} else {
		if (chan_a) {
			--pulse_cnt[0];
		} else {
			++pulse_cnt[0];
		}
	}
}

static void IRAM_ATTR encoder1_chan_a(void *arg)
{
	(void) arg;

	const uint32_t chan_a = gpio_get_level(ENCODER1_CHAN_A);
	const uint32_t chan_b = gpio_get_level(ENCODER1_CHAN_B);

	if (chan_a) {
		if (chan_b) {
			--pulse_cnt[1];
		} else {
			++pulse_cnt[1];
		}
	} else {
		if (chan_b) {
			++pulse_cnt[1];
		} else {
			--pulse_cnt[1];
		}
	}
}
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

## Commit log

2021-10-06 #4 Continue initializing DBW firmware
    Adds framework for rate task timing (and 1Hz example)
2021-10-06 Set up initial ros environment
    parent 4081a56bd7b877d2bc04f8b5a07f49acf18a8710
    author Henry Son <son3@cooper.edu> 1632944686 -0400
    committer dmezh <daniel.mezhiborsky@cooper.edu> 1633543301 -0400
    update with ros env setup
    updated readme
    oops not supposed to push your own workspace
    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
    [model-1_4.sdf, model.sdf]
2021-11-08 HWME-14 Add encoder mount files
    [ArmMount^EncoderMountV1.DXF, ArmMount^EncoderMountV2.DXF, EncoderMountV1.SLDASM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]
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2022-03-25 Add move base
    [scooter.urdf]
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2022-03-29 DBW-31 Initial bootloader
    [partitions_igvc.csv]
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2022-04-01 DBW-42 Correct encoder pins
2022-04-02 Resolve DBW-39 "Brake firmware"
2022-04-02 Resolve DBW-44 "Extended base states"
    [base.c]
2022-04-11 moved move_base to nav
    [scooter.urdf]
2022-04-27 dockercompose mounts zed launch pkg and fixed typo in zed2i driver script
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2022-05-16 zed+rtabmap+move_base working
    [scooter.urdf]
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2022-10-06 Move bootloader to dbw/node_bl
    [partitions_igvc.csv]
2022-10-06 something works
    [calibration.yaml, mesh_may29.ply]
2022-10-06 urdf and nice but upside-down novatel odom
    [cuber.urdf]
2022-10-06 base_local_planner working
    [cuber.urdf]
2022-10-06 Freeze post-comp
    [rtabmap.cfg]
2022-10-06 Remove and move
    [model-1_4.sdf, model.sdf]
2022-10-06 Clean up docker/navigation
    [scooter.urdf]
2022-10-06 Clean up docker/rtabmap
    [mesh_may29.ply, rtabmap.cfg]
2022-10-06 Fix py-steering Dockerfile
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2022-11-04 CAN naming consistency (#79)
    * Refactored `ENCF_EncoderData`
    * Respect `ENCF_EncoderData`
    * Refactored and Respected 'ENCR_EncoderData'
    * Refactored and Respected `BRAKE_BrakeData`
    * Refactored and Respected `PB_ParkingBrakeData`
    * Refactored and Respected `DBW_NodeInfo`
    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
2022-11-05 Move brake/encoders/pbmon, fix blink
    [rear_encoder.c]
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2023-01-22 add ROS node to test with arduino cart
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2023-01-26 Move encoders to opencan - encoder ticks are now continuous
2023-01-27 Split builds up by board in platformio.ini, add new board.json
2023-02-02 Added pseudocode for supervisor.c's handling of BRAKE status
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2023-02-07 modify encoder_odom.py to calculate velocity from absolute encoder ticks
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2023-02-09 Swap encoder channels
2023-02-09 Modify stack-start.sh to add techbus and encoder_odom containers, and remove gps
2023-02-09 Create rtabmap_gps.launch and modify rtabmap.launch to subscribe to /encoder_odom topic
2023-02-09 small bug fix in encoder_odom.py
    [encoder_odom.py]
2023-02-10 Use opencan STEER_angleCmd bodge
2023-02-10 mount dev volume into zed container to fix udev priviledge issues
2023-02-10 py-steering fixes
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2023-02-15 fixed ros host in docker compose for encoder_odom node
    [encoder_odom.py]
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2023-03-03 Updated `offset` feature for `temperature` signal in `nodeStatus`
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2023-03-20 #include <esp_attr.h> and don't put IRAM_ATTR on prototypes
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2023-03-24 Bump ember for timer fix
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2023-03-26 Make sure to check `DBW_RawVelocityCommand` for brake and throttle
2023-03-26 Move pio board.jsons and pin defs to CooperUnion/ccmn_defs
2023-03-26 Remove old node_bl
    [partitions_igvc.csv]
2023-03-26 Hello world as ember_bl
    [partitions_igvc.csv]
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2023-03-26 Reboot from firmware for UpdateControl
    [update.py]
2023-03-27 sdkconfig: set minimum esp32-s3 supported hardware revision to 0.1
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2023-03-29 Add support for node v1.2 temp sensor in cuber_base
2023-03-29 Change temperature reporting range from -10,80 to -30,50
2023-03-31 Change temperature message width from 7 bits to 8 bits (#133)
    * Change temperature message width from 7 bits to 8 bits
    * Change core-temp message width back to 7 bits, offset to 31, and error
    temperature to -31
2023-04-01 Rename STEER_SteeringCmd to DBW_SteeringCommand (#132)
    * Rename STEER_SteeringCmd to DBW_SteeringCommand
    * STEER_SteeringCmd -> DBW_SteeringCommand in techbus and test_steering.py
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2023-04-09 Remove #pragma bodge around timer.h in favor of CONFIG_GPTIMER_SUPPRESS_DEPRECATE_WARN
2023-04-24 New Watchdog (#138)
    * Modify watchdog.c in ember
    * Print registers on panic
    * Bump ember for new watchdog
    ---------
2023-04-25 add icp odometry to rtabmap map launch file
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2023-05-18 add calibrate script for zed and lidar alignment
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2023-05-18 add new gazebo worlds and launch files
    [mesh.blend, model-1_2.sdf, model-1_3.sdf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]
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2023-05-21 Add 10 bit PWM precision for 2.0 throttle node
2023-05-21 Fix opencan version and RawVelocityCommand
    [ctrl.c]
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2023-05-21 Fix clause for DBW_VelocityCommand in ctrl
    [ctrl.c]
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2023-05-22 Add throttle A and F duty cycle values
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2023-05-22 Correct cycle time for BrakeData
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2023-05-23 Calibrate ODrive if errors are detected
    [steer.c]
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2023-05-23 Fix `cycleTime` for 100Hz `DBWVelocityCommand`
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2023-05-25 Add missing ODrive signals
    [steer.c]
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2023-05-26 Correctly encode `STEER_odriveVelocity`
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2023-05-30 p3d odometry in gazebo
    [gem_gazebo.urdf.xacro, gem_sensors.urdf.xacro]
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2023-06-01 Correct decoding of absolute encoder
    [steer.c]
2023-06-01 Reset setpoint once we enter closed loop control
    [steer.c]
2023-06-02 Correct floating point promotion
    [steer.c]
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2023-06-02 Reboot ODrive before performing a full calibration
    This ensures that errors on the ODrive get cleared.
    [steer.c]
2023-06-02 Don't request ODrive controller mode
    The ODrive retains the controller mode between reboots.
    [steer.c]
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2023-06-02 Clear errors instead of rebooting
    [steer.c]
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2023-06-02 lane_detection container added and live feed otput from zed camera is working
2023-06-02 Add bootloader wiring to all CCMN 2.0B envs
2023-06-02 Detects a Barrel and how far from the barrel the camera is
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2023-06-03 Loosen timing and fix typo in bl update.py
    [update.py]
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2023-06-03 Add modules for barrel, tire, and lane detection in detection container
2023-06-03 Correct calculation of average velocity
    [ctrl.c]
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2023-06-04 Add functionality to adjust PID gains over CAN
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2023-09-09 Apply new `pre-commit` hooks
    [calibration.yaml, cuber.urdf, model.sdf]
2023-10-22 Apply `yamlfix` and `yamllint` `pre-commit` hooks
    [calibration.yaml]
2024-02-01 Revert "Set `SCONSFLAGS`"
    This reverts commit `0700e7cc18c6b28330265f2a4cdb53dc29bfcdd0`.
    This currently interferes with PlatformIO's use of SCons.
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2024-02-02 change adc channel from io 8 to io 5
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2024-02-10 Forcefully remove in case `libprebuilt.a` doesn't exist
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2024-02-23 Apply IIR filter for pressure sensor at 10kHz
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2024-02-23 fix ps adc channel, add slp and flt pins
2024-02-29 printing unfiltered and filtered data for both ADC channels
2024-02-29 removed motor current sensor from adc for purposes of taking data
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2024-03-01 corrected limit switch logic and gpios
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2024-03-02 modded limit switch debounce, needed to make deturministic
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2024-03-05 modified bbc motor logic with ternary statements, sleeping motor if hit limit switch
2024-03-05 add testing script for brake motor and tuning PID
2024-03-05 can change the PID gains for the BRAKE and CTRL nodes through CAN
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2024-03-08 flipped logic for left wheel so forwards is forwards
    [ctrl.c]
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2024-03-13 Remove `node_fw`
    Goodbye PlatformIO! You will forever have a special spot in my heart <3
    [partitions_igvc.csv]
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2024-03-14 Restore bootloader builds
    [partitions_igvc.csv]
2024-04-10 flipped encoder pin
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2024-05-25 motor polarity flip
2024-05-31 adjust min and max bbc adc readings to map from 0-100 on percent
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2024-06-01 Resolve issues with `iir_filter()`
    [bbc.c]
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2024-06-01 Add MATLAB script to generate filter coefficients
    [40p_1000ms_80kHz.csv]
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2024-06-01 tuned velocity gains uphill/downhill, satisfied with performance, could probably use more ki but rather be slow to respond than overshoot
    [ctrl.c]
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2024-06-02 correct inner loop angle inputs
    [steer.c]
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2025-04-09 Revert esp-idf version from v5.4-dev to stable v5.3.2 (#217)
    Quick fix to resolve GPIO warnings that come from the `ledc` library in v5.4
    release of esp-idf.
